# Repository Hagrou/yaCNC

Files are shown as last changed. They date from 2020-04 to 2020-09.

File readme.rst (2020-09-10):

##########
Projet CNC
##########

Construction de la CNC 
======================

Branchements et configuration de la carte cnc-shield
----------------------------------------------------

A la réception de l'arduino cnc shield, l'absence de doc nous laisse
un peu coi... Heureusement, le blog Protoneer_ donne de précieuses
informations.

Branchement des moteurs
~~~~~~~~~~~~~~~~~~~~~~~

Il faut simplement brancher les 4 moteurs sur les slots :

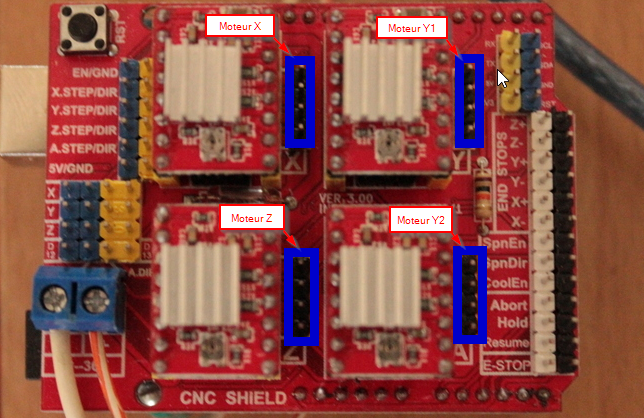
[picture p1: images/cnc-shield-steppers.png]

       
   Branchement des moteurs

Le sens des cables n'a pas d'importance, il faut juste veiller à ce
qu'ils soient tous branchés pareils (bleu en haut par exemple). Le
réglage du sens des mouvement se fera ultérieurement.

Synchroniser les deux moteurs sur l'axe Y
~~~~~~~~~~~~~~~~~~~~~~~~~~~~~~~~~~~~~~~~~

Comme nous avons 2 axes Y commendés par 2 moteurs, nous les
synchronisons en ajoutons 2 jumpers (en bleu sur la figure)

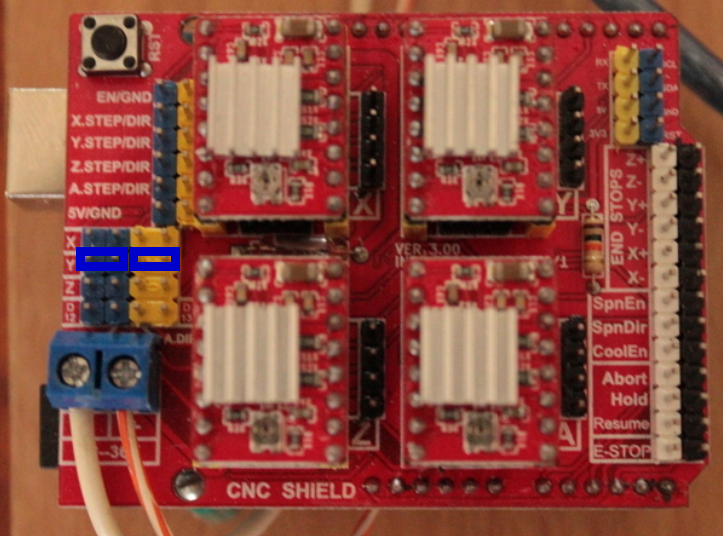
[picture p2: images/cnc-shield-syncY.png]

       
   Jumper à placer pour synchroniser les moteurs Y

Il faut ensuite brancher les 2 moteurs sur les connecteurs Y et A.

Activation des capteurs de fin de course
~~~~~~~~~~~~~~~~~~~~~~~~~~~~~~~~~~~~~~~~

Les capteurs de fin de course sont importants. Ils permettent de
recalibrer les positions des 3 axes en cas de glissement lors d'un
précédent mouvement.

3 capteurs sont nécessaire, à brancher au niveau de la cate (END STOPS).

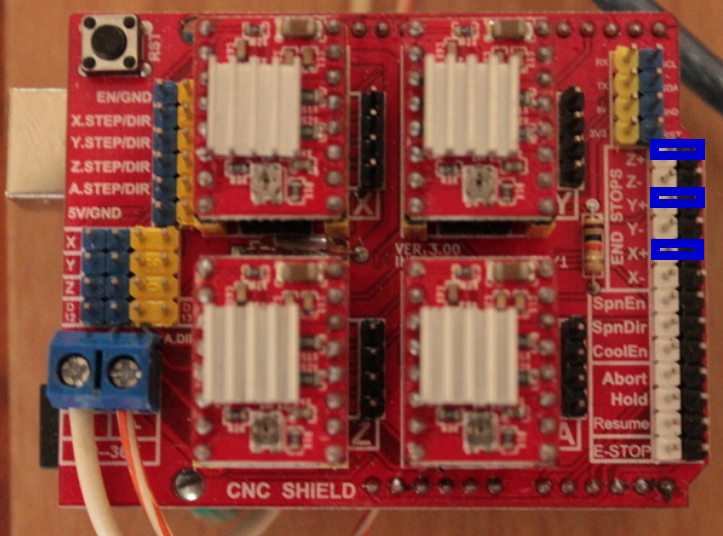
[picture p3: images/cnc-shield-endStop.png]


Controller sur un raspberry
---------------------------

L'idée est de pouvoir controller en temps réel notre CNC. Pour cela, nous allons utiliser un raspberry surlequel nous installons

Deport d'écran
--------------

Pour éviter de rester dans le garage pendant que la CNC travail, on va
installer le serveur vncserver sur le raspi afin de pouvoir travailler
en déport d'écran !

Sur le raspi

    $ sudo apt install vnc4server
    $ vncpasswd
    Password:
    Verify:
    Would you like to enter a view-only password (y/n)? y
    Password:
    Verify:

    $ vncserver -localhost no

Sur la machine de controles

    $ remmina

2 parties :

$ sudo apt install java-common

- Controle des moteurs via arduino  => GRBL (exécution de gcode)

- Execution de jcode et controle de l'arduibno bCNC

Controle Arduino (GRBL)
------------------------

L'ensemble des mouvements est réalisé par de l'interprétation de
langage, le gcode. Nous allons utiliser le soft GRBL pour cela.

Compilation de GRBL
~~~~~~~~~~~~~~~~~~~

Installation de l'environnement de compilation
~~~~~~~~~~~~~~~~~~~~~~~~~~~~~~~~~~~~~~~~~~~~~~

Il faut tout d'abord mettre en place l'environnement de Compilation_ pour pouvoir configurer GRBL.

	$ sudo apt update
	$ sudo apt upgrade

Installation de gcc-avr

	$ sudo apt install gcc-avr binutils-avr avr-libc gdb-avr

Tout est prêt pour compiler GRBL. Il faut tout d'abord le récupérer
sur [github](https://github.com/grbl/grbl).

	$ mkdir grbl
	$ unzip grbl-master.zip
	$ cd grbl-master
	$ make clean; make all

Configuration 'on-line' de GRBL
~~~~~~~~~~~~~~~~~~~~~~~~~~~~~~~

La configuration de la CNC se trouve par tatonnement (j'ai pas trouvé
mieux dans mon cas...). Du coup, j'ai utilisé le programme bCNC pour
faire bouger les différents axes et la console serie de python pour
tester les paramètres.

L'idée est trouver l'ensemble des paramètres 'on-line' puis ensuite de
les "bruler" dans une compilation (seconde partie).

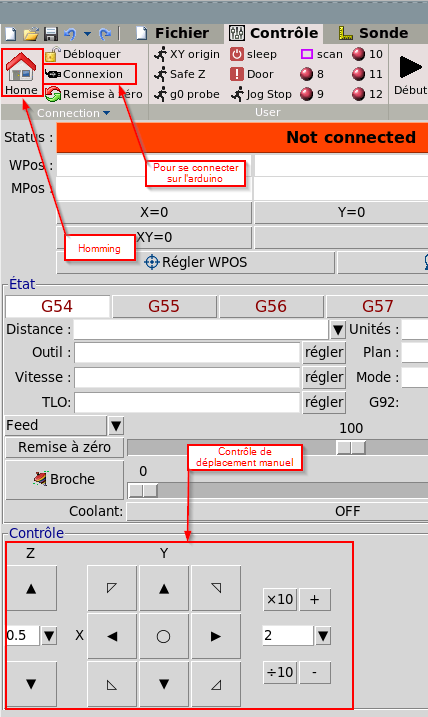
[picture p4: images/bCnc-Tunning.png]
 

Pour trouver le port usb de connexion avec l'arduino il suffit
d'utiliser la commande python :

  $ python -m serial.tools.list_ports

On peut ensuite utiliser le terminal serie de python en envoyer des
commandes

    $ python -m serial.tools.miniterm /dev/ttyACM0 115200

    avec:
      - /dev/ttyACM0 : le port usb/serie de ma configuration
      - 115200       : vitesse de transmisison serie

- Direction de déplacement

  Il faut tout d'abord configurer le sens de déplacement des 3
  axes. Certains blogues proposent d'inverser la cablage des moteurs
  pour obtenir le sens approprié. En fait, le paramètre $3 permet par
  la configuration d'un masque de définir le sens de chaque
  déplacement.

  Aussi, tous les moteurs sont branchés dans le même sens. Et j'ai
  appliqué le mask suivant pour obtenir les bons déplacements :
  
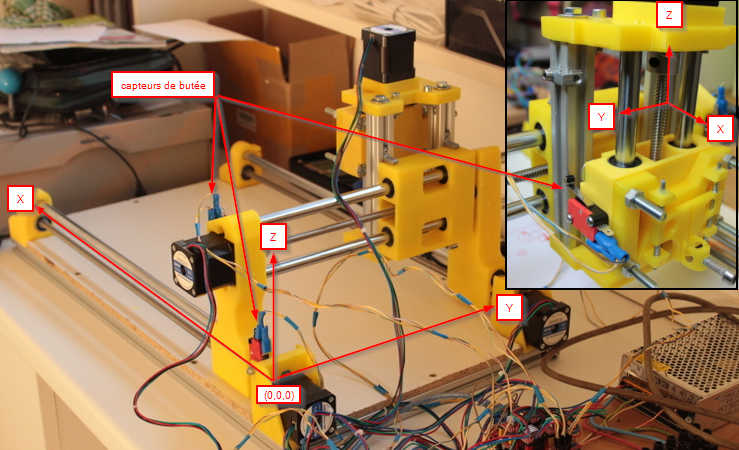
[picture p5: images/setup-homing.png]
  
	  
  $3=4 (dir port invert mask:00000100)
  
  - 00000001: déplacement -X
  - 00000010: déplacement -Y
  - 00000100: déplacement -Z

- Homing

  La capacité de la CNC a se recalibré sur un point de référence (0,0,0)
  est crucial. Le principe consiste en faisant déplacer chaque axe
  jusqu'a ce qu'il rencontre le capteur de butée.

  Dans notre cas, les butées sont positionnées en (0,0,0), ce qui veut
  dire que pour trouver les butées la CNC doit faire décroitre les
  positions de chaque axe. 
  
  

  Etonnament, ce n'est pas le comportement par défaut de GRBL. Pour le
  moment je préfère retrouver les origines de mes axes (?). Aussi nous
  devons modifier le paramètre homing-dir-invert-mask_ ($23) lui
  donner la valeur 3 (qui correspond à la valeur de mask:00000011)
  avec :
  
     - 00000001: recherche butée -X
     - 00000010: recherche butée -Y
     - 00000100: recherche butée -Z

  Note : la butée en Z est placée en haut de l'axe Z afin d'éloigné l'outil
  de la piece qui vient d'être créée.

  Il faut également activer le mode homing cycle en affectant 1 au
  paramètre homing-cycle-boolean_ ($22).

- Nombre de pas / mm

  Il faut définir la correspondance entre le nombre de pas du moteur
  et la distance parcourue :

  :math:`\frac{nbr\_pas * micro\_pas}{pas\_de\_vis}`
	 
  Dans mon cas:
  
  - l'angle d'un pas de mon moteur est de 1.8 degree. Il faut donc 200
    pas pour faire tour complet.

  - je n'ai pas configuré les micro_pas
    
  - j'ai un pas de vis de 2 mm

  Je dois donc entrer les valeurs : :math:`\frac{200*1}{2}=100`

  ::

      $100=100 (x, step/mm)
      $101=100 (y, step/mm)
      $102=100 (z, step/mm)
  
- Limites de déplacement

  Afin d'éviter d'emplafonner les limites de la CNC, nous allons
  maintenant configurer les déplacement max de chaque axe.

  Les coordonnées de déplacements sont affichées en exécutant la
  commande '?' dans la console : <Idle,MPos:0.000,0.000,0.000,WPos:0.000,0.000,0.000>

  On a :

  - MPos:0.000,0.000,0.000
    
    Ce sont les coordonnés par rapport au 0 de la machine (initialisé après un homming par exemple).
    
  - WPos:0.000,0.000,0.000

    Ce sont les coordonnées de travail, relative à MPos. Ce repère
    sera initialisé en fonction du positionnement de la pièce à
    réaliser.

    $130=150.000 (x max travel, mm)
    $131=390.000 (y max travel, mm)
    $132=67.000 (z max travel, mm)

    $20=1
    (!) Max travel => Mpos?
    (!) pb avec Z: -67 pas possible. Max > 0
   https://github.com/BullzLabz/GRBL-French-wiki/blob/master/content/Configuring-Grbl-v0.9-fr.md
    => 0z => bas mais il faut que le homming monte.
    - Si homming => Z=0 at home

    => il faut inverser le sens de Z!?
    
Pour cela, j'ai suivi un [tuto](https://www.cours-gratuit.com/cours-arduino/tutoriel-arduino-et-grbl-avec-cnc-shield-v3-pdf) plutot sympa.

bCNC: https://fablabo.net/wiki/BCNC/controle

Résumé
~~~~~~

Voici l'ensemble des paramètres à appliquer :

   ::
      
     $3=4
     $22=1
     $23=3
     $100=150 
     $101=390 
     $102=-67

La personnalisation se fait à partir du fichier grbl/default.h qui
fait un include sur grbl/default/default_<CNC>.h
#### Fichier default.h
Par default, il pointe sur le fichier grbl/default/default_generic.h

On va donc "dériver" grbl/default/default_generic.h en grbl/default/default_yacnc.h

::

    $ cp grbl/grbl-master/grbl/defaults/defaults_generic.h grbl/grbl-master/grbl/defaults/defaults_yacnc.h

- faire point le default.h dessus. Editer le fichier drbl/default.h et changer ajouter :

    ::

        #ifdef DEFAULTS_YACNC
           #include "default/defaults_yacnc.h"
        #endif

Configuration de default_yacnc.h
~~~~~~~~~~~~~~~~~~~~~~~~~~~~~~~~~

Le fichier default_yacnc.h (Yet Another CNC) va contenir l'ensemble
des caractéristiques de notre CNC. Pour cela il faut :

https://lebearcnc.com/configurer-et-parametrer-grbl/

Les premiers paramètres sont liés aux caractéristiques des moteurs pas à pas ainsi que les pas de vis:

::

    #define MOTOR_STP 200 // number of step per turn (Angle de pas : 1.8 degree)
    #define MICRO_STP 16  // Micro stepping 1/16 step ? TODO: valide 1?
    #define SCREW_PITCH_MM 2 // Pas de 2mm pour les vis sans fin

Ce qui permet de déduire le nombre de tour pour avancer d'1 mm :

::

    // Grbl generic default settings. Should work across different machines.
    #define DEFAULT_X_STEPS_PER_MM (MICRO_STP*MOTOR_STP/SCREW_PITCH_MM)
    #define DEFAULT_Y_STEPS_PER_MM (MICRO_STP*MOTOR_STP/SCREW_PITCH_MM)
    #define DEFAULT_Z_STEPS_PER_MM (MICRO_STP*MOTOR_STP/SCREW_PITCH_MM)

On définit ensuite la course max de chaque axe (mm) :

::

    #define DEFAULT_X_MAX_TRAVEL 240.0 // mm // (130) TODO
    #define DEFAULT_Y_MAX_TRAVEL 480.0 // mm // (131) TODO
    #define DEFAULT_Z_MAX_TRAVEL 75.0 // mm // (132) TODO

Les vitesses max :

::

    #define DEFAULT_X_MAX_RATE 380.0 // (110) mm/min
    #define DEFAULT_Y_MAX_RATE 380.0 // (111) mm/min
    #define DEFAULT_Z_MAX_RATE 220.0 // (112) mm/min

Enfin on active les detecteurs de fin de course

::

    #define DEFAULT_HOMING_ENABLE 1  // activation des detecteurs de fin de course
    #define DEFAULT_HOMING_DIR_MASK 0 // move positive dir
    #define DEFAULT_HOMING_FEED_RATE 25.0 // (24) Vitesse lente/précise (mm/min)
    #define DEFAULT_HOMING_SEEK_RATE 380.0 // (25) Vitesse de déplacement jusqu'à déclencher les capteurs mm/min
    #define DEFAULT_HOMING_DEBOUNCE_DELAY 250 // (26) msec (0-65k) Tps de filtrage de rebond du capteur
    #define DEFAULT_HOMING_PULLOFF 1.0 // (27) mm decalage des fins des capteurs                                     

Configuration de config.h
~~~~~~~~~~~~~~~~~~~~~~~~~
Pour activer la configuration yacnc, il faut remplacer la ligne :

	  #define DEFAULTS_GENERIC

par

      #define DEFAULTS_YACNC

Compilation
~~~~~~~~~~~

Trouver le port usb de connexion avec l'arduino

    $ python -m serial.tools.list_ports

Puis lancer la compilation :

    	$ make

Flasher l'arduino

    $ make flash

    https://github.com/gnea/grbl/wiki/Grbl-v1.1-Configuration#20---soft-limits-boolean

Lancer un terminal serie :

    $ python -m serial.tools.miniterm /dev/ttyACM0 115200

Notes Impression dessin
-----------------------

- Position en (0,0,0)
  => Remonte en 2z, puis descend à -1z  (profondeur 1, déplacement sécurisé +2)

- Limites Soft: Depend de WPOS? 
Slicing d'une piece
-------------------

http://www.metabricoleur.com/t401-cn-du-dessin-a-la-piece-debutants
   
------

.. _Compilation: http://maxembedded.com/2015/06/setting-up-avr-gcc-toolchain-on-linux-and-mac-os-x/

.. _Protoneer: https://blog.protoneer.co.nz/arduino-cnc-shield-v3-00-assembly-guide/

.. _homing-cycle-boolean: https://github.com/gnea/grbl/wiki/Grbl-v1.1-Configuration#22---homing-cycle-boolean

.. _homing-dir-invert-mask: https://github.com/gnea/grbl/wiki/Grbl-v1.1-Configuration#23---homing-dir-invert-mask

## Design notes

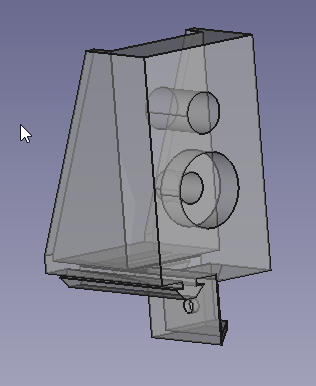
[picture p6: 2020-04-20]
mechanical/framework/corner-left.png

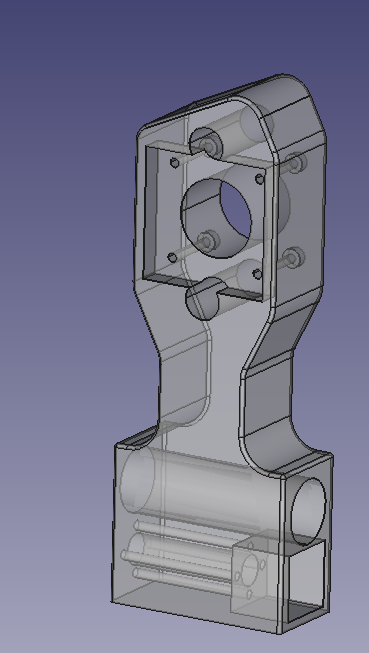
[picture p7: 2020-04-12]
mechanical/axes/axe-y-left.png

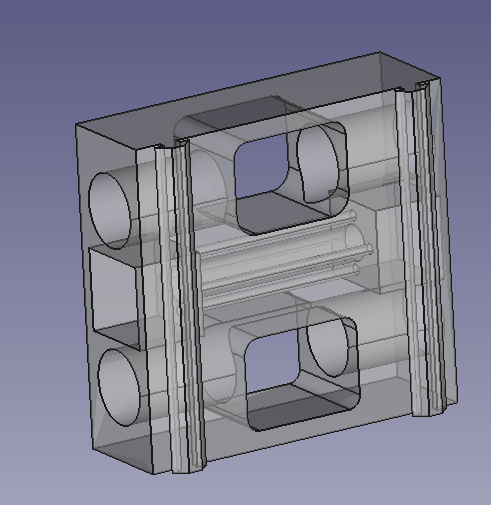
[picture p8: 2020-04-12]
mechanical/axes/sled-back.png

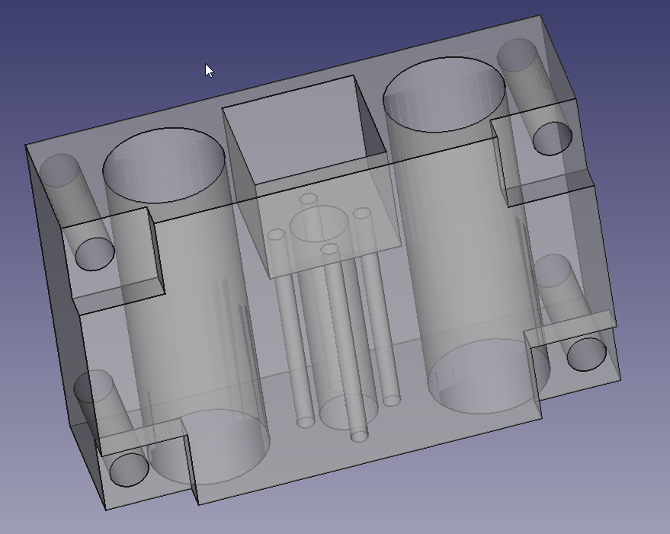
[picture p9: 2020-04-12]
mechanical/axes/sled-tools.png

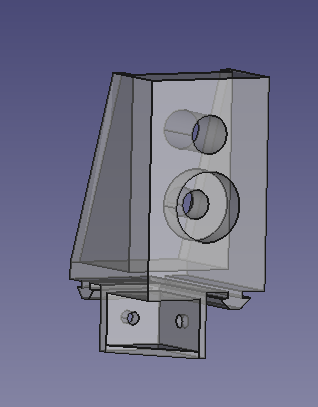
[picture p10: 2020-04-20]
mechanical/framework/corner-right.png

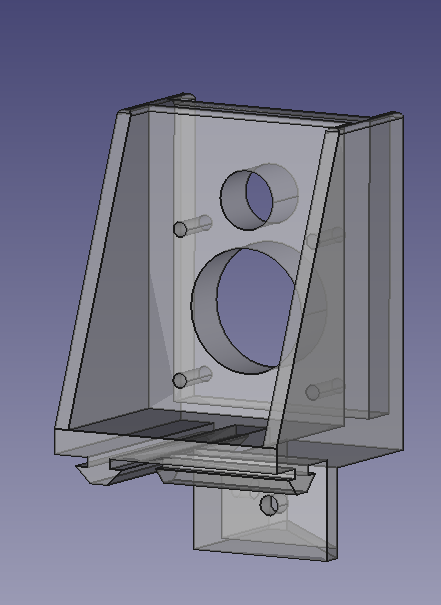
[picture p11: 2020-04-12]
mechanical/framework/corner-left-engine.png

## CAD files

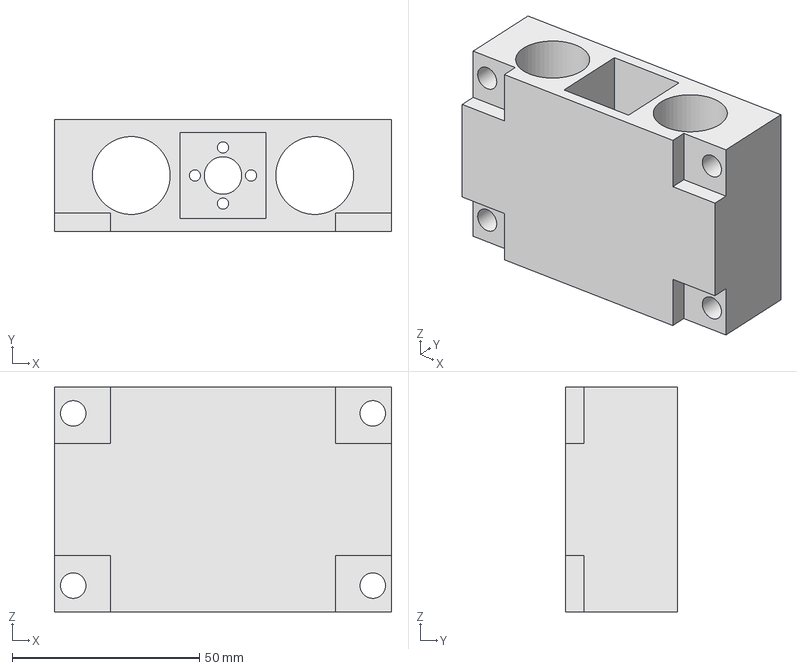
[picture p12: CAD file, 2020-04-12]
mechanical/axes/sled-tools.FCStd
90.0 x 30.0 x 60.0 mm

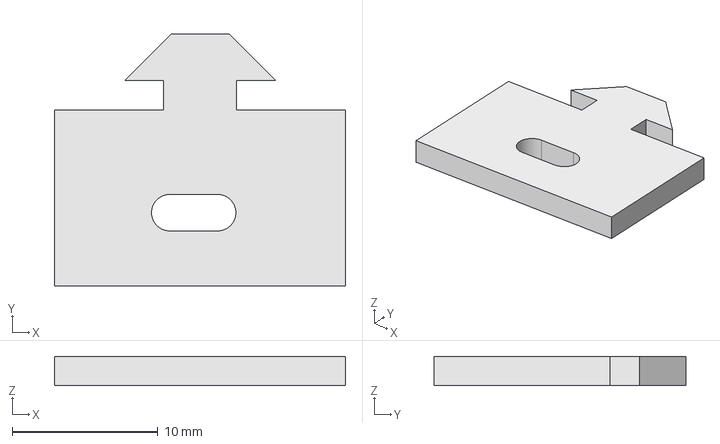
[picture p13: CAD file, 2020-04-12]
mechanical/draft/test-groove.FCStd
20.0 x 17.3 x 2.00 mm

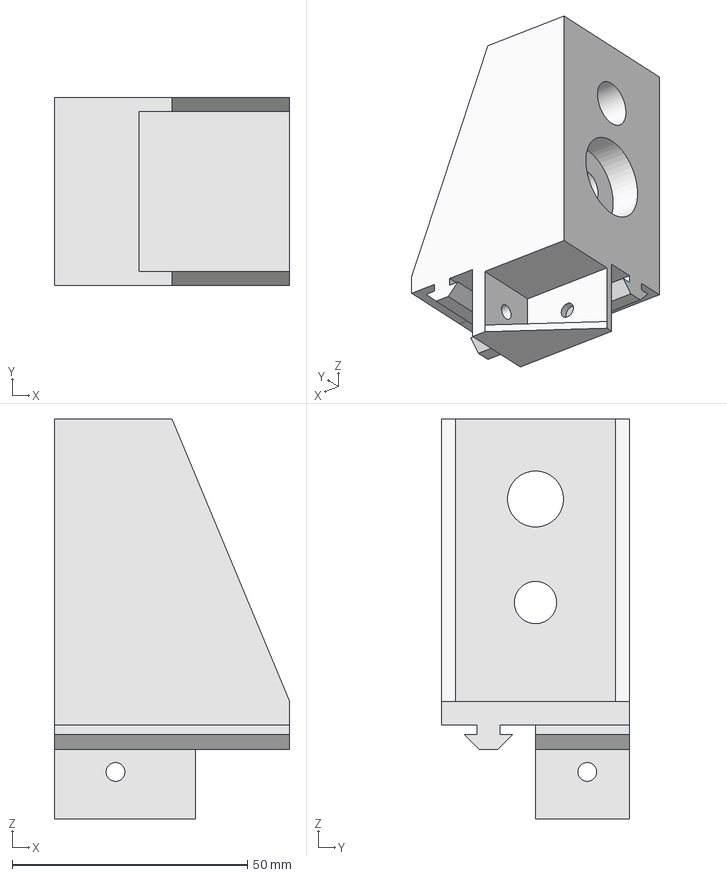
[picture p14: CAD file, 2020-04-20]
mechanical/framework/corner-right.FCStd
50.0 x 40.0 x 85.0 mm

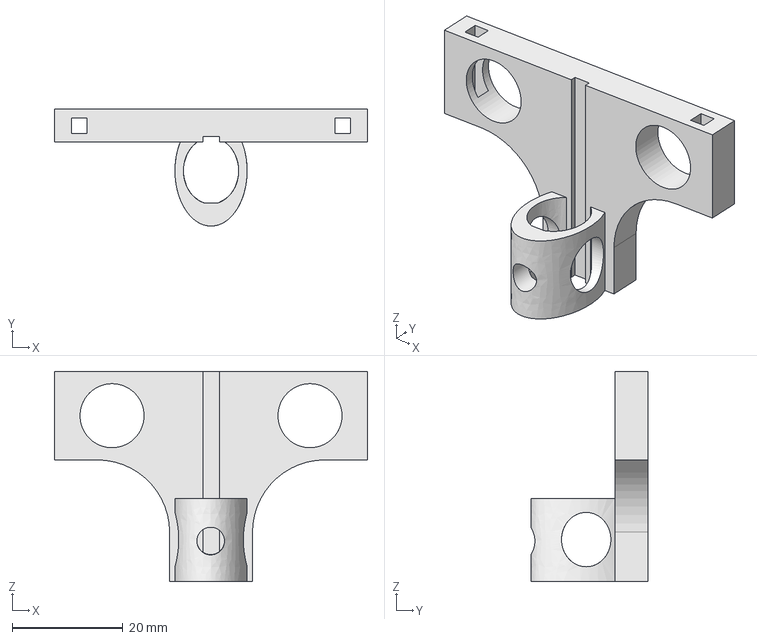
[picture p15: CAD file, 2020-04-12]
mechanical/tools/tool-pencil.FCStd
56.6 x 21.2 x 38.0 mm

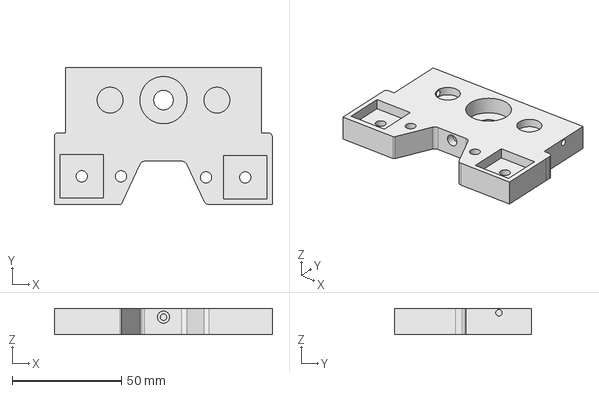
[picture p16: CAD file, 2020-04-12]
mechanical/axes/sled-bottom.FCStd
100.0 x 62.9 x 12.0 mm

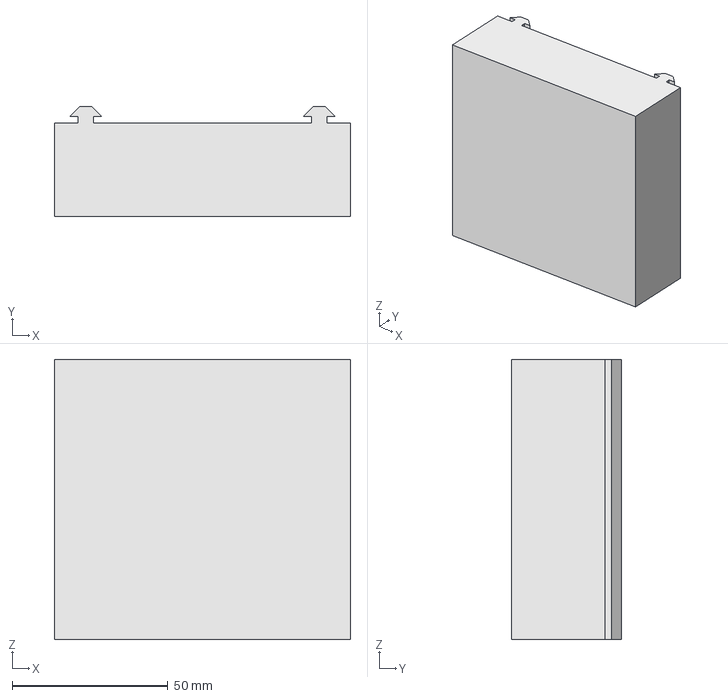
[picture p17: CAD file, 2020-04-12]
mechanical/draft/groove.FCStd
95.0 x 35.2 x 90.0 mm

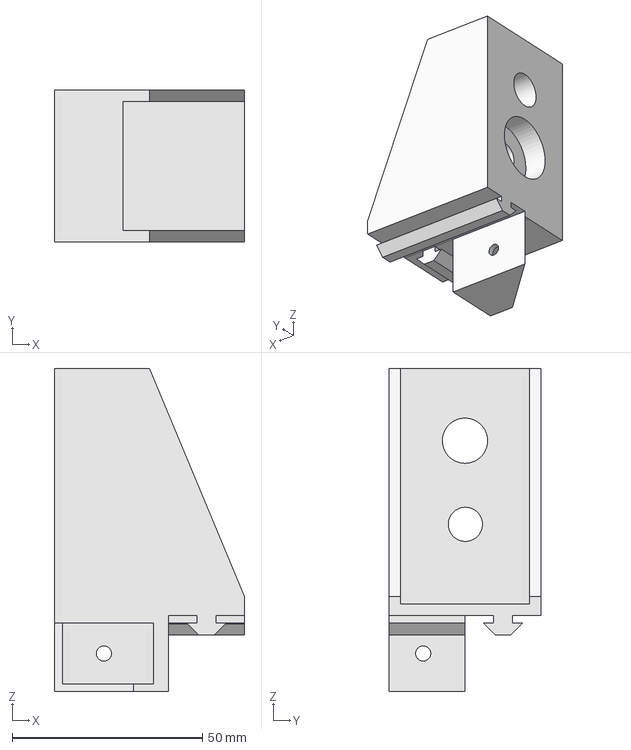
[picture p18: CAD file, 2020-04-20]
mechanical/framework/corner-left.FCStd
50.0 x 40.0 x 85.0 mm

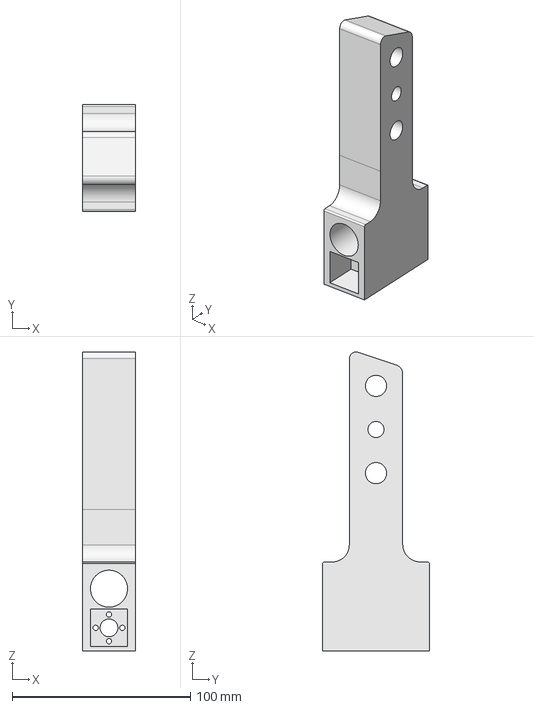
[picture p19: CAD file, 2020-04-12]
mechanical/axes/axe-y-right.FCStd
30.0 x 60.0 x 167.9 mm

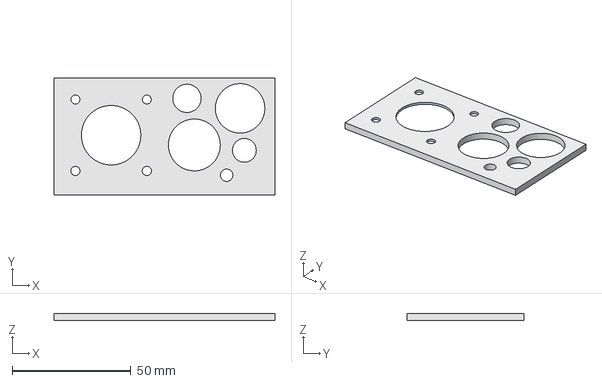
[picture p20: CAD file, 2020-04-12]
mechanical/draft/test-gabari.FCStd
92.9 x 49.1 x 3.00 mm

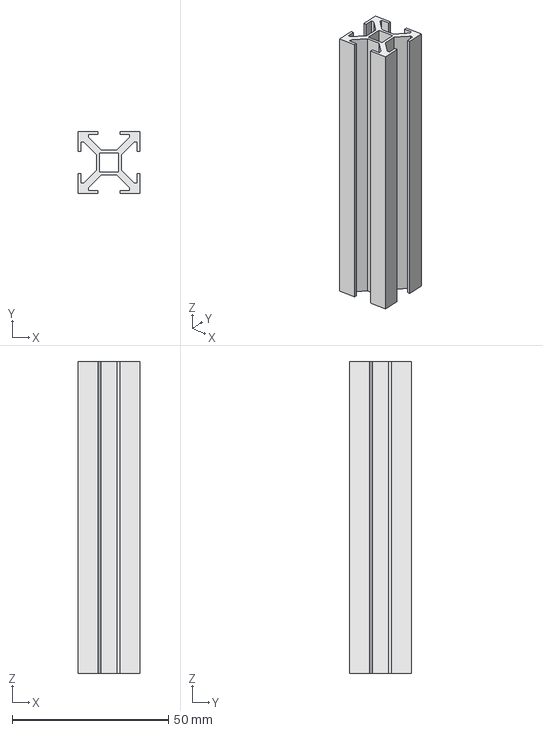
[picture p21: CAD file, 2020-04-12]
mechanical/framework/track.FCStd
20.0 x 20.0 x 100.0 mm

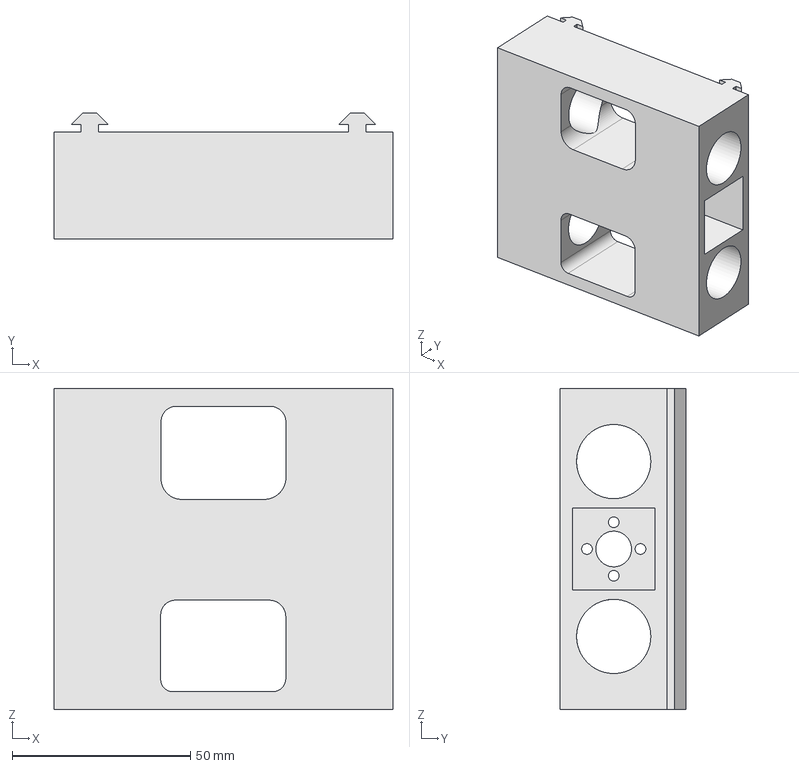
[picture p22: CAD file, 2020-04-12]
mechanical/axes/sled-back.FCStd
95.0 x 35.2 x 90.0 mm

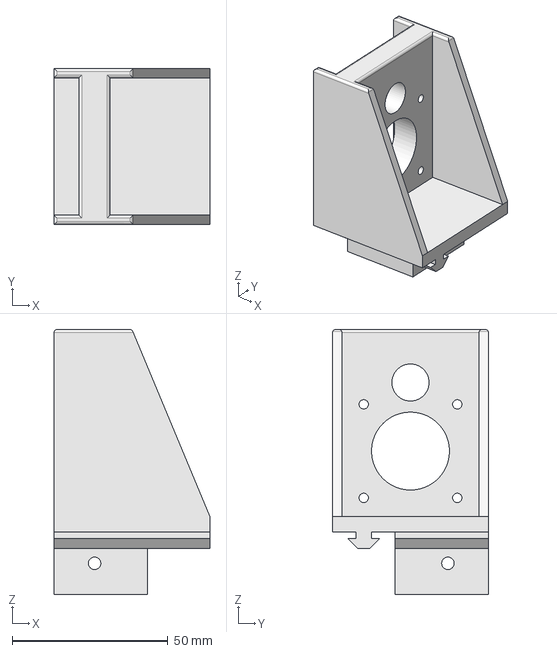
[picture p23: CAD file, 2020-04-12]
mechanical/framework/corner-left-engine.FCStd
50.0 x 50.0 x 85.0 mm

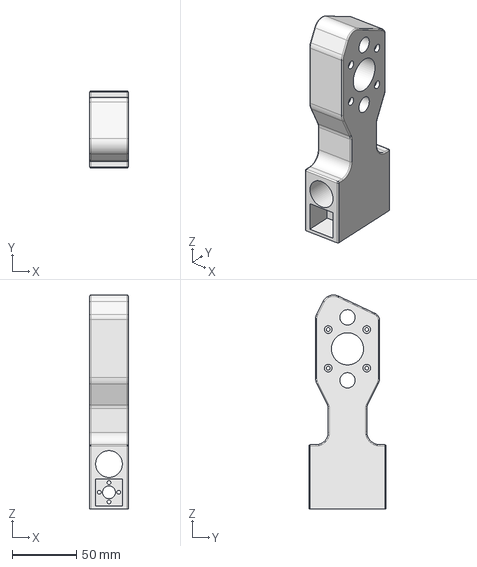
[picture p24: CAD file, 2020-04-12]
mechanical/axes/axe-y-left.FCStd
30.0 x 60.0 x 166.5 mm

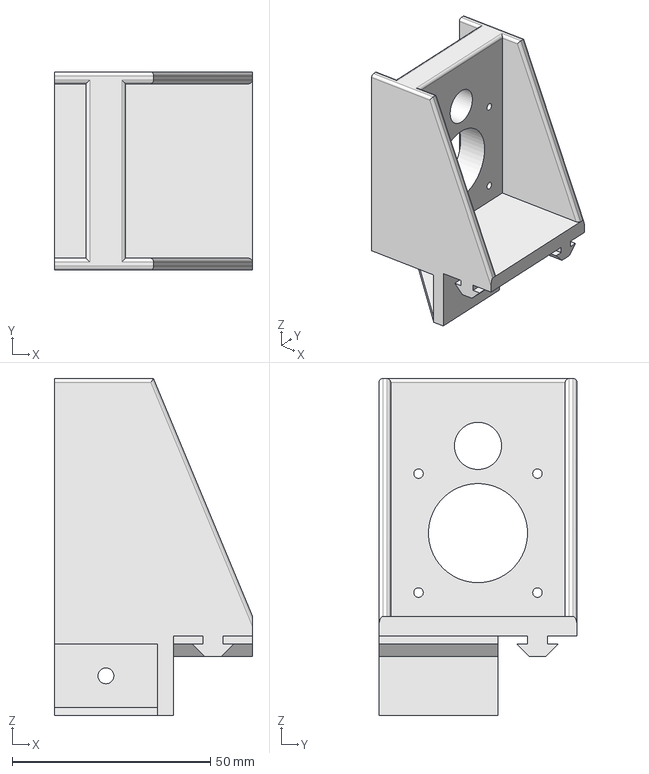
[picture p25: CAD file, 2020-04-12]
mechanical/framework/corner-right-engine.FCStd
50.0 x 50.0 x 85.0 mm

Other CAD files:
mechanical/axes/sled-top.FCStd
mechanical/framework/corner-left.stl
mechanical/framework/corner-right.stl

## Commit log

2020-04-20 + corner left
    [corner-left.FCStd]
2020-04-20 + corner right
    [corner-left.stl, corner-right.FCStd, corner-right.stl]
